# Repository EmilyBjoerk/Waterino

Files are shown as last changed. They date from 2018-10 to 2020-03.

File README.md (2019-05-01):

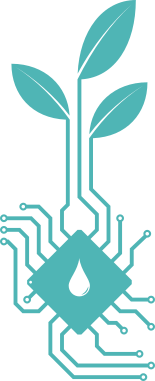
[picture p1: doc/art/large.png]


# Waterino

Waterino is a DIY multi-pot home watering system. Multiple pots are connected together by daisy chaining "nodes" together with a "root" node providing power, monitoring and water. The daisy chaining means that the chain can be re-ordered when moving pots around and that there is a minimal amount of wire-mess as opposed to a star-network.

Each "node" consists of an integrated moisture/temperature sensor and control logic, a pump/valve and an optional overflow sensor to safe guard from causing damage to the surrounding by watering too much.

The "root" node consists of a water reservoir, a Raspberry Pi and power delivery. The RPi monitors the nodes with heart-beat and listens for error reports over I2C, provides a web server with logging and monitoring and can be setup to send email alerts if an error is detected or if the water level in the reservoir is low.

# System Diagram
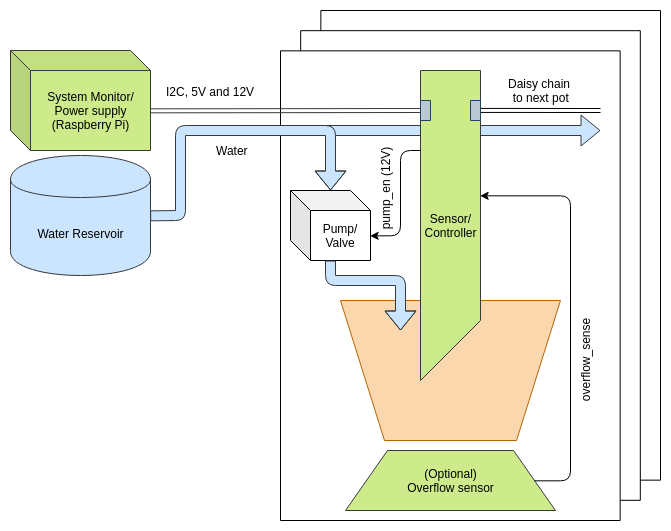
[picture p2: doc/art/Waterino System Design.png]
Waterino Logo


# Building on Debian
You'll need the following:

```sudo apt install build-essential git cmake clang clang-tools gcc-avr avr-libc libgmock-dev avrdude```

Building and running unit-tests:

```
cd firmware/test
mkdir build
cd build
cmake ..
make test
```

or ``` make && ./unit-tests ``` for a more detailed output.

Viewing code coverage of unit tests (first build as above):

```
cd firmware/test/build
../../codecov.sh [path_to_file.cpp]
```

Building binary:

```
cd firmware/src
mkdir build
cd build
cmake ..
make
```

Viewing binary stats (after building as above):

```
cd firmware/src/build
make size
make sizes
make disassemble && cat probe.lst
```

# Design
## Measurement
The Waterino uses capacitive soil moisture and temperature sensor integrated in the node PCB.

The PCB has a coplanar capacitor pattern where the soil is the dielectric. The capacitance of the coplanar capacitance depends on how much water is in the soil as the dielectric constant of water dominates that of other material in the soil. We measure the capacitance by charging it through a known resistance and measuring the time it takes to charge to a known value which gives the capacitance.

There is also a NTC thermistor inside the soil that we use to measure the soil temperature. The temperature is used for correcting the slight temperature dependency of the moisture-capacitance relation.

## Control
The user specifies the desired watering period in hours, the maximum time the pump may be active and the threshold moisture level when the pump will activate.
Each time the measured moisture drops below the threshold the pump activates. When the pump activates the onboard PID will measure the time from the last pump activation and use that in relation to the desired watering period to compute if it should give more or less water than it did last time.
Note that if a too long period is specified in relation to the water retaining capacity of the soil. It may be impossible to achieve the desired period. This would cause the PID give more and more water, causing the pot to eventually overflow. The maximum pump activation time is aimed at preventing this failure mode. 

## Logging
The node keeps a small in memory log of the last few measurements and other important information. The root will poll the nodes for their respective logs and keep a longer term history slice the data and serve it over HTTP.

## Communication
The node will print debug information over 5V UART at 38400 baud, 8 bits data, 0 parity, 1 stop bit.

The node is a i2c master and slave device. It can be addressed to read the log, set parameters and control the node in other ways. It can also send to the general call address and write a special magic sequence followed by it's own unique slave address, this acts as a mutex device for activating a pump so that only one pump is active at a time, thanks to the i2c bus arbitration and unique slave addresses. This is makes sure that the water preasure available is always the same for the pumps, one can imagine if all pumps were to activate at once, the feed line from the reservoir would probably not have enough flow rate and the later pumps in the daisy chain wouldn't get any water.

## Safety
There are a few things that can go wrong... First, it's an electronic device near water that can possibly output 12V@5A 60W of power. A number of safety measures are implemented to hopefully prevent the device from harming itself, you or the plants.
In no particular order:

* Nodes will detect if too much water was given to the plant by two electrodes which you put in the saucer below your plant. If these electrodes conduct electricity the pump is automatically killed and the node will limit the next pump activation to the time it took for it to overflow this time but make it 5% shorter. To prevent a fluke from limiting the pump activation to way too short times, it will carefully try to recover the maximum pump duration to the user set duration over time, backing off if it detects overflow again.
* It will detect if the water level in the reservoir is low and email you.
* It will prevent the time the pump is active from going below a minimum time.
* A PTC fuse on each node will trip if the power on that node shorts out, and a PTC fuse on the root will like wise protect the system.
* Nodes will detect upon restart if it was killed by the fuse tripping and emit a visual alert and push an error to the root. The node will resume normal operation after being power cycled once, allowing a human to inspect what went wrong before trying again.

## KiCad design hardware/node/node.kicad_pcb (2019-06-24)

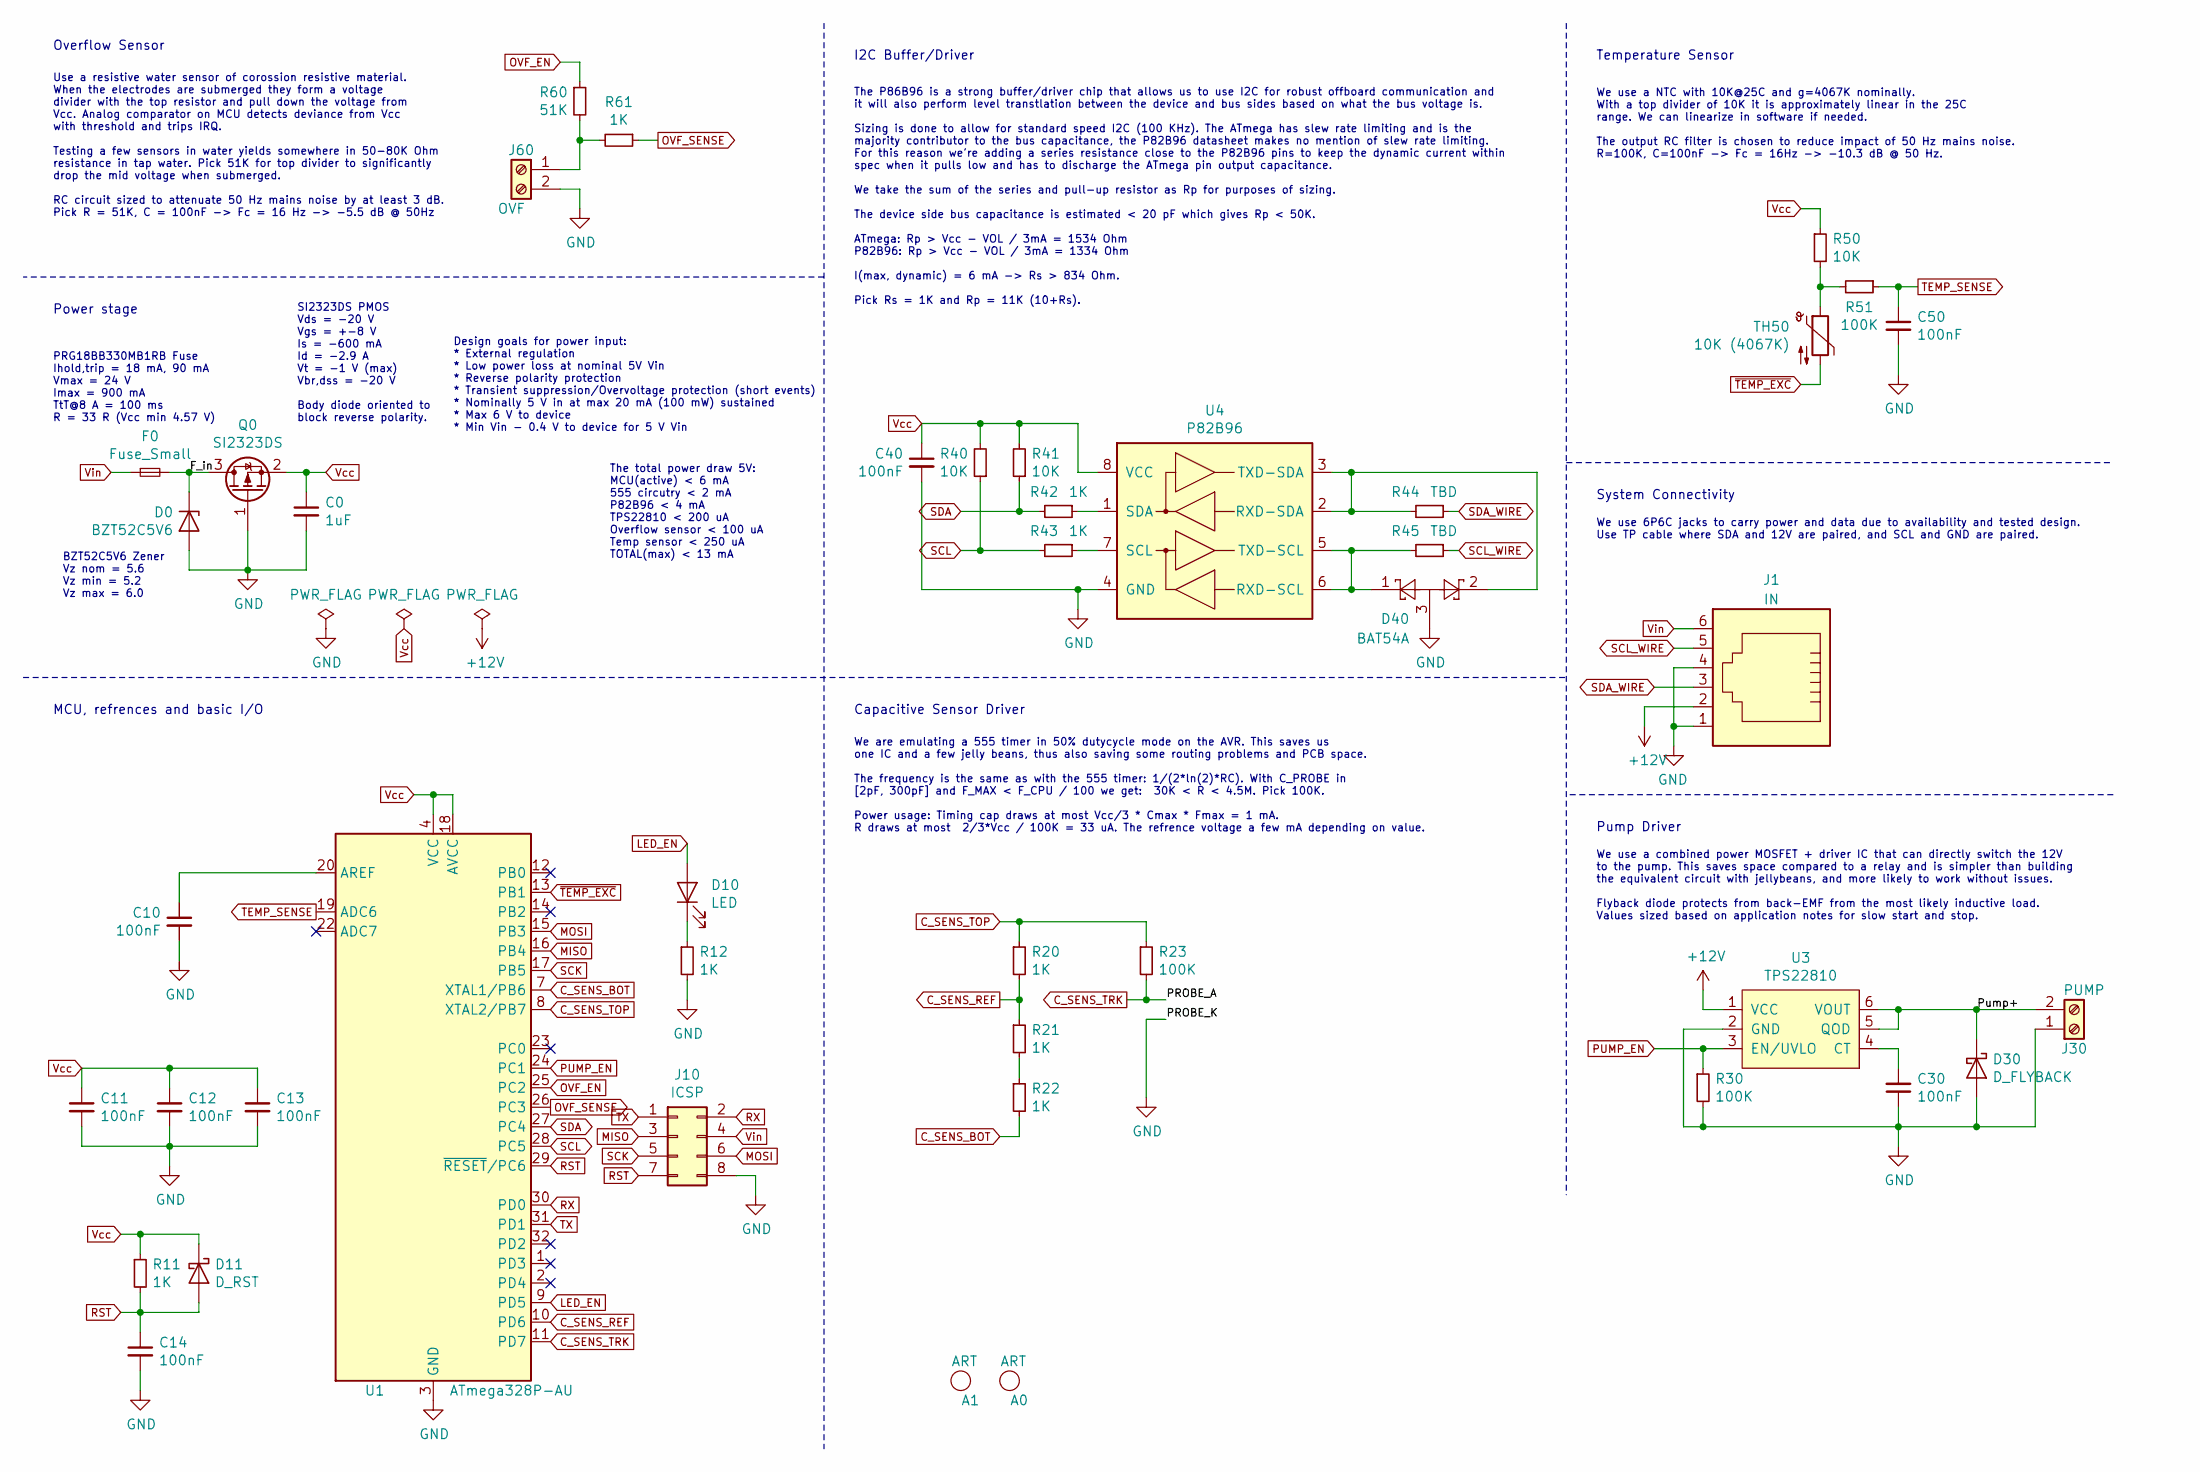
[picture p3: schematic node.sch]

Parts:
A0: ART; waterino_small_12_3mm
A1: ART; OSH_7_3mm
C0: 1uF; C_0603_1608Metric_Pad1.05x0.95mm_HandSolder
C10, C11, C12, C13, C14, C30, C40, C50: 100nF; C_0603_1608Metric_Pad1.05x0.95mm_HandSolder
D0: BZT52C5V6; D_SOD-123
D10: LED; LED_0603_1608Metric
D11: D_RST; D_SOD-123
D30: D_FLYBACK; D_SOD-123
D40: BAT54A; SOT-23
F0: Fuse_Small; Fuse_0603_1608Metric_Pad1.05x0.95mm_HandSolder
J1: IN; RJ12_Amphenol_54601
J10: ICSP; PinHeader_2x04_P2.54mm_Vertical
J30: PUMP; TerminalBlock_RND_205-00045_1x02_P5.00mm_Horizontal
J60: OVF; TerminalBlock_RND_205-00045_1x02_P5.00mm_Horizontal
Q0: SI2323DS; SOT-23W_Handsoldering
R11, R12, R20, R21, R22, R42, R43, R61: 1K; R_0603_1608Metric_Pad1.05x0.95mm_HandSolder
R23, R30, R51: 100K; R_0603_1608Metric_Pad1.05x0.95mm_HandSolder
R40, R41, R50: 10K; R_0603_1608Metric_Pad1.05x0.95mm_HandSolder
R44, R45: TBD; R_0603_1608Metric_Pad1.05x0.95mm_HandSolder
R60: 51K; R_0603_1608Metric_Pad1.05x0.95mm_HandSolder
TH50: 10K (4067K); R_0603_1608Metric_Pad1.05x0.95mm_HandSolder
U1: ATmega328P-AU; TQFP-32_7x7mm_P0.8mm
U3: TPS22810; SOT-23-6_Handsoldering
U4: P82B96; TSSOP-8_3x3mm_P0.65mm

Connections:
+12V: J1.2, U3.1 (VCC)
/F_in: D0.1 (K), F0.2, Q0.3 (D)
/Pump+: D30.1 (K), J30.2, U3.5 (QOD), U3.6 (VOUT)
C_SENS_BOT: R22.2, U1.7 (XTAL1/PB6)
C_SENS_REF: R20.2, R21.1, U1.10 (PD6)
C_SENS_TOP: R20.1, R23.1, U1.8 (XTAL2/PB7)
C_SENS_TRK: R23.2, U1.11 (PD7)
GND: C0.2, C10.2, C11.2, C12.2, C13.2, C14.2, C30.1, C40.2, C50.2, D0.2 (A), D30.2 (A), D40.3, J1.1, J1.4, J10.8, J30.1, J60.2, Q0.1 (G), R12.2, R30.2, U1.3 (GND), U1.5 (GND), U1.21 (GND), U3.2 (GND), U4.4 (GND)
LED_EN: D10.2 (A), U1.9 (PD5)
MISO: J10.3, U1.16 (PB4)
MOSI: J10.6, U1.15 (PB3)
unnamed: C10.1, U1.20 (AREF)
unnamed: C30.2, U3.4 (CT)
unnamed: D10.1 (K), R12.1
unnamed: D40.1, R45.2, U4.5 (TXD-SCL), U4.6 (RXD-SCL)
unnamed: D40.2, R44.2, U4.2 (RXD-SDA), U4.3 (TXD-SDA)
unnamed: J60.1, R60.2, R61.2
unnamed: R21.2, R22.1
unnamed: R42.1, U4.1 (SDA)
unnamed: R43.1, U4.7 (SCL)
unnamed: R50.2, R51.2, TH50.1
OVF_EN: R60.1, U1.25 (PC2)
OVF_SENSE: R61.1, U1.26 (PC3)
PUMP_EN: R30.1, U1.24 (PC1), U3.3 (EN/UVLO)
RST: C14.1, D11.2 (A), J10.7, R11.2, U1.29 (~RESET~/PC6)
RX: J10.2, U1.30 (PD0)
SCK: J10.5, U1.17 (PB5)
SCL: R40.1, R43.2, U1.28 (PC5)
SCL_WIRE: J1.5, R45.1
SDA: R41.1, R42.2, U1.27 (PC4)
SDA_WIRE: J1.3, R44.1
TEMP_SENSE: C50.1, R51.1, U1.19 (ADC6)
TX: J10.1, U1.31 (PD1)
Vcc: C0.1, C11.1, C12.1, C13.1, C40.1, D11.1 (K), Q0.2 (S), R11.1, R40.2, R41.2, R50.1, U1.4 (VCC), U1.6 (VCC), U1.18 (AVCC), U4.8 (VCC)
Vin: F0.1, J1.6, J10.4
~TEMP_EXC: TH50.2, U1.13 (PB1)

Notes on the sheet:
Power stage
Design goals for power input: * External regulation * Low power loss at nominal 5V Vin * Reverse polarity protection * Transient suppression/Overvoltage protection (short events) * Nominally 5 V in at max 20 mA (100 mW) sustained * Max 6 V to device * Min Vin - 0.4 V to device for 5 V Vin
BZT52C5V6 Zener Vz nom = 5.6 Vz min = 5.2 Vz max = 6.0
SI2323DS PMOS Vds = -20 V Vgs = +-8 V Is = -600 mA Id = -2.9 A Vt = -1 V (max) Vbr,dss = -20 V Body diode oriented to block reverse polarity.
PRG18BB330MB1RB Fuse Ihold,trip = 18 mA, 90 mA Vmax = 24 V Imax = 900 mA TtT@8 A = 100 ms R = 33 R (Vcc min 4.57 V)
We use 6P6C jacks to carry power and data due to availability and tested design. Use TP cable where SDA and 12V are paired, and SCL and GND are paired.
System Connectivity
Overflow Sensor
Use a resistive water sensor of corossion resistive material. When the electrodes are submerged they form a voltage divider with the top resistor and pull down the voltage from Vcc. Analog comparator on MCU detects deviance from Vcc with threshold and trips IRQ. Testing a few sensors in water yield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
Pump Driver
We use a combined power MOSFET + driver IC that can directly switch the 12V to the pump. This saves space compared to a relay and is simpler than building the equivalent circuit with jellybeans, and more likely to work without issues. Flyback diode protects from back-EMF from the most likely induct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
Temperature Sensor
We use a NTC with 10K@25C and g=4067K nominally. With a top divider of 10K it is approximately linear in the 25C range. We can linearize in software if needed. The output RC filter is chosen to reduce impact of 50 Hz mains noise. R=100K, C=100nF -> Fc = 16Hz -> -10.3 dB @ 50 Hz.
I2C Buffer/Driver
The P86B96 is a strong buffer/driver chip that allows us to use I2C for robust offboard communication and it will also perform level transtlation between the device and bus sides based on what the bus voltage is. Sizing is done to allow for standard speed I2C (100 KHz). The ATmega has slew rate lim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
Capacitive Sensor Driver
MCU, refrences and basic I/O
The total power draw 5V: MCU(active) < 6 mA 555 circutry < 2 mA P82B96 < 4 mA TPS22810 < 200 uA Overflow sensor < 100 uA Temp sensor < 250 uA TOTAL(max) < 13 mA
We are emulating a 555 timer in 50% dutycycle mode on the AVR. This saves us one IC and a few jelly beans, thus also saving some routing problems and PCB space. The frequency is the same as with the 555 timer: 1/(2*ln(2)*RC). With C_PROBE in [2pF, 300pF] and F_MAX < F_CPU / 100 we get: 30K < R < 4.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

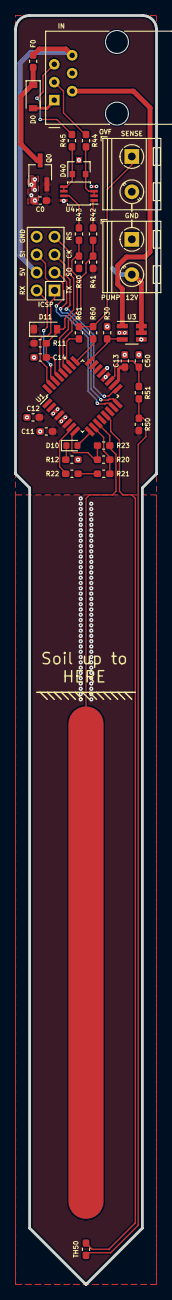
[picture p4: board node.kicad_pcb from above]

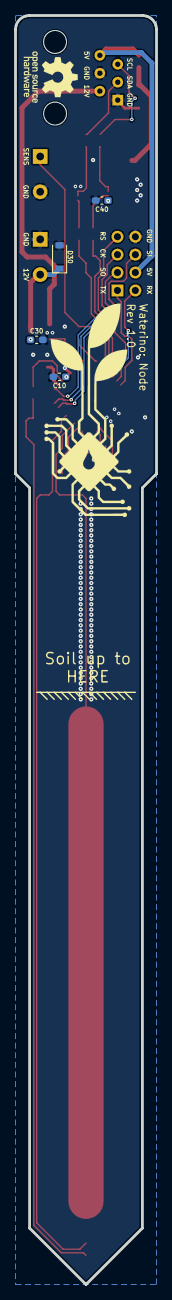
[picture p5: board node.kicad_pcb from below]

Board: 2 copper layers, 20.0 x 180.0 mm, 43 parts (6 on the bottom side), 36 nets.

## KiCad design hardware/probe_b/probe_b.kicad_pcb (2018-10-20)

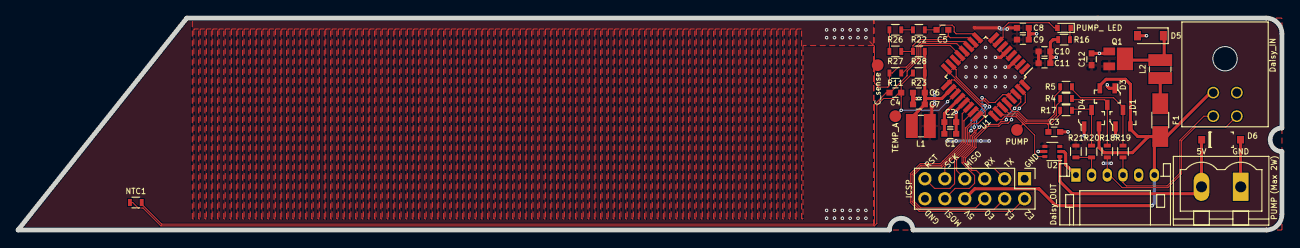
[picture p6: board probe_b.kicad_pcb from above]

Board: 2 copper layers, 161.0 x 27.0 mm, 46 parts (0 on the bottom side), 37 nets.

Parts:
C1, C3, C6, C9, C10: 10nF; C_0603
C2, C4, C5, C7, C8, C11: 100nF; C_0603
C12: 1µF; C_0603
D1, D3, D4: BAT54S-7-F; SOT-23-3
D2: PUMP_ LED; D_0603
D5: BZT52C5V6; D_SOD-123
D6: MBR0520LT1G; SOD-123
F1: 0ZCJ0050FF2G; Fuse_SMD1206_HandSoldering
J1: ICSP; Pin_Header_Straight_2x06_Pitch2.54mm
J2: PUMP; Measurement_Point_Round-SMD-Pad_Small
J3: PUMP; PhoenixContact_MSTBVA-G_02x5.00mm_Vertical
J4: C_sense; Measurement_Point_Round-SMD-Pad_Small
J5: Daisy_OUT; JST_PH_S6B-PH-K_06x2.00mm_Angled
J6: Daisy_IN; Molex_Microfit3_Header_02x02_Angled_43045-040x
J7: TEMP_A; Measurement_Point_Round-SMD-Pad_Small
L1, L2: 10uH; 1210
NTC1: R; R_0603
Q1: SI2323DS; SOT-23-Power
R4, R5, R17, R18, R19, R20: 150R; R_0603
R11: 1M; R_0603
R16: 1K; R_0603
R21: 10K; R_0603
R22, R26, R27, R28: 100K; R_0603
R23: 15K; R_0603
U1: ATMEGA328P-AU; TQFP-32_7x7mm_Pitch0.8mm
U2: MIC94090; SOT-363_SC-70-6

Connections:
/Csense: J4.1, R11.2, U1.11
AVcc: C6.1, C7.1, L1.2, R23.1, R28.2, U1.18
DBG_A0: J1.6, U1.24
DBG_A1: J1.4, U1.23
DBG_A2: J1.2, U1.22
GND: C1.2, C2.2, C3.2, C6.2, C7.2, C8.2, C9.2, C10.2, C11.2, C12.2, D1.1, D3.1, D4.1, D5.2, D6.A, J1.1, J1.12, J3.1, J5.1, J5.5, J6.2, Q1.1, R16.2, U1.3, U1.5, U1.21, U2.2, U2.5
MISO: J1.7, U1.16
MOSI: J1.10, U1.15
unnamed: C1.1, C2.1, U1.20
unnamed: D1.3, R5.1, R19.2
unnamed: D2.1, R16.1
unnamed: D3.3, R4.1, R18.2
unnamed: D4.3, R17.1, R20.2
unnamed: D5.1, L2.2, Q1.3
unnamed: D6.K, J3.2, U2.1
unnamed: F1.2, L2.1
unnamed: J5.2, R20.1, R21.2
unnamed: J5.3, J6.4, R18.1
unnamed: J5.4, J6.3, R19.1
unnamed: R22.2, R26.1
unnamed: R26.2, R27.1
OVRFLW_SENSE: C3.1, R17.2, U1.26
PUMP: J2.1, U1.25, U2.6
PWRLED: D2.2, U1.7
RC_EN: R11.1, U1.12
RC_REF: C5.1, R27.2, R28.1, U1.10
RST: J1.11, U1.29
RX: J1.5, U1.30
SCK: J1.9, U1.17
SCL: R5.2, U1.28
SDA: R4.2, U1.27
TEMP+: C4.2, J7.1, NTC1.1, R23.2, U1.19
TX: J1.3, U1.31
Vcc: C8.1, C9.1, C10.1, C11.1, C12.1, L1.1, Q1.2, R21.1, U1.4, U1.6, U2.4
Vin: D1.2, D3.2, D4.2, F1.1, J1.8, J5.6, J6.1
~RC_EXC: C5.2, R22.1, U1.9
~TEMP_EXC: C4.1, NTC1.2, U1.13

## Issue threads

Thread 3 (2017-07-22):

Add RC-Oscillator calibration mode.

EmilyBjoerk, 2017-07-22:

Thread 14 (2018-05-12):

Write wiki page on assembling a Waterino

EmilyBjoerk, 2018-05-12:
A wiki page should exist that details which gerbers, BOM, other peripherals, firmware etc should be built and the steps that are necessary to validate the PCB, burn the fuse bits, calibrate the oscillator and start using the Waterino.

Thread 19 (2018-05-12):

Refactor pump and moisure measurement logic so that it can be unit-tested on other archs.

EmilyBjoerk, 2018-05-12:
We should refactor the pump and moisture measurement code, actually pretty much the core logic of the project should be unit-testable on PC. This requires encapsulating the HW specific bits in an interface that can be swapped.

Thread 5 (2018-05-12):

Adjust PCB layout: Give more clearance to power lines

EmilyBjoerk, 2018-05-12:
The high current traces on the PCB should have more clearance. Should be at least 1.25mm which should be up to 300V for uncoated surface conductors below 3500m above sea level.

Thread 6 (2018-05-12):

Adjust PCB layout: Limit current to 20A@12V

EmilyBjoerk, 2018-05-12:
The selected fuse: [MF-LSMF300/24X](https://www.bourns.com/docs/Product-Datasheets/mflsmf.pdf) has a max current of 20A, we should see if we can somehow design the PCB to limit the current to 20A through passives.

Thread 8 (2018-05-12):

Validate fuse actually works as intended.

EmilyBjoerk, 2018-05-12:
Use the lab power supply to test that the fuse will actually trip as expected when the pump leads are shorted.

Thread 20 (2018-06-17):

Probe B needs slew rate limiting on SDA/SCL

EmilyBjoerk, 2018-06-17:
I missed the fine print in the ATtiny manual that the SDA/SCL pins do not have slew rate limiting. The necessary components to achieve this should be added to the PCB for the next revision.

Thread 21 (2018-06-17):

Probe B has wrong net on electrodes

EmilyBjoerk, 2018-06-17:
The bottom electrode (as per the PCB layout) has MOIST+ assigned to it, while it in fact should have the middle of R4 and R5 assigned to it.

Closed 2018-07-12.

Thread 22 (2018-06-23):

Change soil measurement circuit

EmilyBjoerk, 2018-06-23:
Due to the way the avr input pins work, when the micro sleeps (i.e.. most of the the time) the pins will be shorted to ground. meaning that most of the time the pins are connected to the micro which means that any esd into the ground risks damaging the micro.

Appropriate protections should be added.

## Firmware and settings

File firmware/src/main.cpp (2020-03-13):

/*
This file houses only top level globals and the trivial main loop.

The actual business logic is encapsulated in the Application class in order for it to be testable.
 */
#include "application.hpp"
#include "hardware.hpp"
#include "xtd_uc/eeprom.hpp"

// This could be (and in general best practice should be) in the main body, but that
// makes the whole object part of the stack instead of the .data section meaning that
// it is harder to estimate the total required memory of the application. For this
// reason it's actually better to have globals in this case.
Application app;

int main() {
  while (true) {
    app.execute_loop();
  }
}

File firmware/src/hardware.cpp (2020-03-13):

/*
 * Both ends of a 1:2 ratio voltage divider are connected to GPIO pins.
 * The midpoint of the voltage divider is connected to the positive pin
 * of the analog comparator. The top pin is charging an RC net and the
 * output of the RC net is the negative pin of the analog comparator.
 *
 * When the divider is positively oriented (top pin +, bottom pin -) then
 * the positive pin of the comparator is 2/3 VCC and the RC net is being
 * charged from 0 to VCC. One the output of the RC net crosses 2/3 VCC
 * The analog comparator raises an IRQ, swapping the top and bottom pin
 * voltages, changing the positive pin voltage to 1/3 VCC and the RC
 * net starts to discharge from 2/3 VCC to 1/3 VCC and the IRQ trips again
 * swapping the pins and so the output of the RC net will oscillate between
 * 1/3 and 2/3 VCC. This is analoguous to a 555 timer in astable 50% duty
 * cycle mode.
 *
 * On the discharge and charge IRQ from the analog comparator we will toggle
 * the T1 pin manually to cause the TIMER/COUNTER1 (which has been suitably
 * configured) to count up one.
 *
 * On TIMER/COUNTER1 overflow we will stop the the counter, break the
 * charge/discharge cycle, and measure how many CPU clockcycles it took for
 * TIMER/COUNTER1 (which is a 16 bit timer) to overflow. Based on this we
 * know the frequency that the RC net oscillated with.
 *
 * The number of CPU clock cycles it took to count up 2^16 relates to the
 * frequency, F, like so: F = 2^16/cycles.
 *
 * This gives the sensed capacitance as F = 1 / (2*ln(2)*R*C)
 * or C = cycles / (2*ln(2)*R*2^16). (#1)
 *
 * We'll assume that the influence of noise on the RC net is low enough to
 * not affect the frequency of the output.
 *
 * The capacitance of the RC net will consist of a parasitic capacitance
 * to the ground plane along the trace to the sensort track and behind
 * the sensor track. We assume this parasitic capacitance has a negligible
 * temperatur dependency compared to the other parts of the sensor in
 * contact with water. This is motivated by the fact that water has around
 * 80 times higher dielectric constant than air and 20 times higher than FR4,
 * and that the separation from the ground plane is relatively high (1.6 mm).
 * A small part of the sensor track is above the ground and dependent on the
 * humidity and temperature. Again here we will assume that the variance
 * of this capacitance due to humidity and temperature will be dominated by
 * the variance of the capacitance of the sensor in contact with the soil
 * and water in the soil.
 *
 * For the above reasons we consider the total capacitance sensed as:
 * C(m,t) = Ck + Cs(m,t) where m is the soil moisture level and t is the
 * temperature of the soil. We know that capacitance is a linear function
 * of the dielectric value regardless of geometry. We know that the dielectric
 * of water depends on the temperature (non linearly).
 *
 * So we can express Cs(m,t) as: A + B*m*T(t). Where T is the temperature
 * dependency of the water's dielectric value. However we can bake A into
 * Ck and rename B as Cs and thus we get:
 *
 * C(m,t) = Ck + Cs*m*T(t)
 *
 * Let's take two calibration points at temperature: t = t_cal. We'll assume
 * that soil can never have less moisture content than the absolute humidity
 * of the air. So our "dry" reference is free air (at some humidity). And
 * our "wet" refrence is with the sensor submerged in water to the same level
 * as the soil will be when in use.
 *
 * Then we have: Cair = C(m_min, t_cal) and Cwater = C(m_max, t_cal).
 *
 * And if we have a measurement of C(m=M,t=t_cal) as C we can solve for 'm' as:
 *
 * m = (C - Cair) / (Cwater - Cair)
 *   = /Substitute and simplify/
 *   = (M*T(t=t_cal) - m_min*T(t_cal))/(m_max*T(t_cal) - m_min*T(t_cal))
 *   = (M*T(t=t_cal)/T(t_cal) - m_min)/(m_max - m_min)
 *
 * So if we let C' = C * T(t_cal)/T(t) and do the above exercise again but let
 * 't' be a free variable, we end up with:
 *
 * m = (M - m_min + E)/(m_max - m_min)
 * E = Ck/Cs*(T(t_cal)/T(t) -1)
 *
 * We know T(t) and can compute it. And because T(t) varies slowly with 't',
 * T(t_cal)/T(t) ~= 1 for t_cal close to 't' and Ck is small compared to Cs
 * using C' = instead of C will yield a smaller error for m than using C directly.
 *
 * Using (#1) above to convert from cycles to capacitance we can see that if
 * the calibration points are also taken as cycle counts, the constant factor
 * 1/(2*ln(2)*R*2^16) will cancel out.
 *
 * So the final formula for 'm':
 *
 * m = (cycles*T(t_cal)/T(t) - cycles_air) / (cycles_water - cycles_air), m = [0,1].
 *
 * Note that it is possible for m to be slightly outside the above ranget due
 * to the fact that we have ignored the (small) dependency on air moisture
 * and air temperature and the approximations made.
 *
 * The calibration points should be taken at the middle of the typical operating
 * temperature range for best accuracy.
 */

#include "hardware.hpp"

#include <avr/interrupt.h>
#include <avr/io.h>
#include <avr/sleep.h>
#include <util/atomic.h>

#include "xtd_uc/adc.hpp"
#include "xtd_uc/blink.hpp"
#include "xtd_uc/chrono.hpp"
#include "xtd_uc/delay.hpp"
#include "xtd_uc/gpio2.hpp"
#include "xtd_uc/sleep.hpp"
#include "xtd_uc/units.hpp"
#include "xtd_uc/utility.hpp"  // bit functions
#include "xtd_uc/wdt.hpp"

constexpr auto ach_not_in_use = uint8_t(0);
constexpr auto ach_overflow = uint8_t(3);
constexpr auto ach_temperature = uint8_t(6);
using pin_overflow_en = xtd::pin<xtd::port_c, 2>;
using pin_overflow_sense = xtd::pin<xtd::port_c, 3>;
using pin_temperature_en = xtd::pin<xtd::port_b, 1>;
using pin_pump_en = xtd::pin<xtd::port_c, 1>;
using pin_pump_led = xtd::pin<xtd::port_d, 5>;
using pin_rc_top = xtd::pin<xtd::port_b, 7>;
using pin_rc_bot = xtd::pin<xtd::port_b, 6>;
using pin_rc_ref = xtd::pin<xtd::port_d, 6>;
using pin_rc_sens = xtd::pin<xtd::port_d, 7>;
using pin_t1 = xtd::pin<xtd::port_d, 5>;

constexpr auto c_overflow_threshold = uint16_t(800 << 6);

volatile HAL::overflow_callback_t g_overflow_cb = nullptr;

ISR(ANALOG_COMP_vect, ISR_NAKED) {
  if (pin_rc_top::test()) {
    // We were charging, start discharging
    pin_rc_top::clr();
    pin_rc_bot::set();
    pin_t1::clr();
  } else {
    // We were discharging, start charging
    pin_rc_top::set();
    pin_rc_bot::clr();
    pin_t1::set();
  }
  reti();
}

ISR(TIMER1_COMPA_vect /*TIMER1_OVF_vect*/) { TCCR1B = 0; }

bool adc_is_free() { return xtd::adc_get_current_ch() == ach_not_in_use; }

void assert_adc_free() {
  if (!adc_is_free()) {
    HAL::fatal(HAL::adc_in_use);
  }
}
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

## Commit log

2017-06-04 Work in progress.
    [backup.kicad_pcb, waterino.kicad_pcb, waterino.sch]
2017-06-19 Finally got it all together and ordered
    [waterino.kicad_pcb, waterino.sch]
2017-07-08 Cleaning up PCB files.
    [backup.kicad_pcb]
2017-07-08 Adding libraries and cleaning up some more.
    [waterino.sch]
2017-07-18 Fixing compile issues and adding a self-test program to test soldering connections on a new waterino.
    [waterino.sch]
2017-07-22 Reworking bits to fit together.
    [main.cpp]
2017-07-22 Adding RX led to the command interpreter.
2018-05-12 Fixing wrong part nr in BOM.
2018-05-12 Fixes #10.
    [waterino.kicad_pcb, waterino.sch]
2018-05-25 Adding schematic for the probe.
    [probe.kicad_pcb, probe.sch, waterino.sch]
2018-05-27 Cleaning up hardware files.
    [core_unit.kicad_pcb, core_unit.sch, probe.kicad_pcb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]
2018-06-15 Probe B as Rev 1 as manufactured.
    [probe_b.sch]
2018-07-12 Fixes #21. Also removes RC filters that made the output impedence too high for the ADC. Changed connector to Micro USB due to cable availabiliy. Changed to a more reasonable inline ferrite and also r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
    [probe_b.kicad_pcb, probe_b.sch]
2018-07-29 Fixing makefile and adding first code fragments for the probe
    [main.cpp]
2018-07-30 Managed to flash blinky on the attiny with arduino as isp.
2018-07-31 Soon ready for first test of i2c on attiny
2018-08-06 Can now get raw data from probe
2018-10-20 Upgrading project to kicad 5.0 and fixing some issues with the last revision.
    [probe_b-2018-09-13-19-54-52.sch, probe_b.kicad_pcb]
2019-03-24 The pump and unit tests code is now WAI and tested.
2019-04-28 WIP, getting calibration done now and fixing issues.
    [application.cpp, hardware.cpp, main.cpp]
2019-06-08 V3 of the node.G
    [core_unit.kicad_pcb, core_unit.sch, node.kicad_pcb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]
2019-06-15 Updating layout of node and art.
    [node.kicad_pcb, node.sch]
2019-06-24 Performing experiment with emulating 555 timer on the ATmega. Seems to work.
2019-07-09 Fixing tests and fixing other issuse with the new code for the new hardware revision.
    [application.cpp, hardware.cpp]
2019-07-19 Fixes several bugs from the initial draft version. Including wrong constant conversion of rc_capacitance, too low max rc_capacitance value, change the rc_counts to not overflow so badly, fix timing i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
    [application.cpp, hardware.cpp, main.cpp]
2019-07-20 Enabling WDT, Fixing inversion of NTC voltage and fixing overflow detection code.
    [application.cpp, hardware.cpp, main.cpp]
2020-03-02 Fix problem in hal::fatal.
    [hardware.cpp]
2020-03-13 More refactoring, fixing bugs and broken unit tests.
    [application.cpp, hardware.cpp, main.cpp]
